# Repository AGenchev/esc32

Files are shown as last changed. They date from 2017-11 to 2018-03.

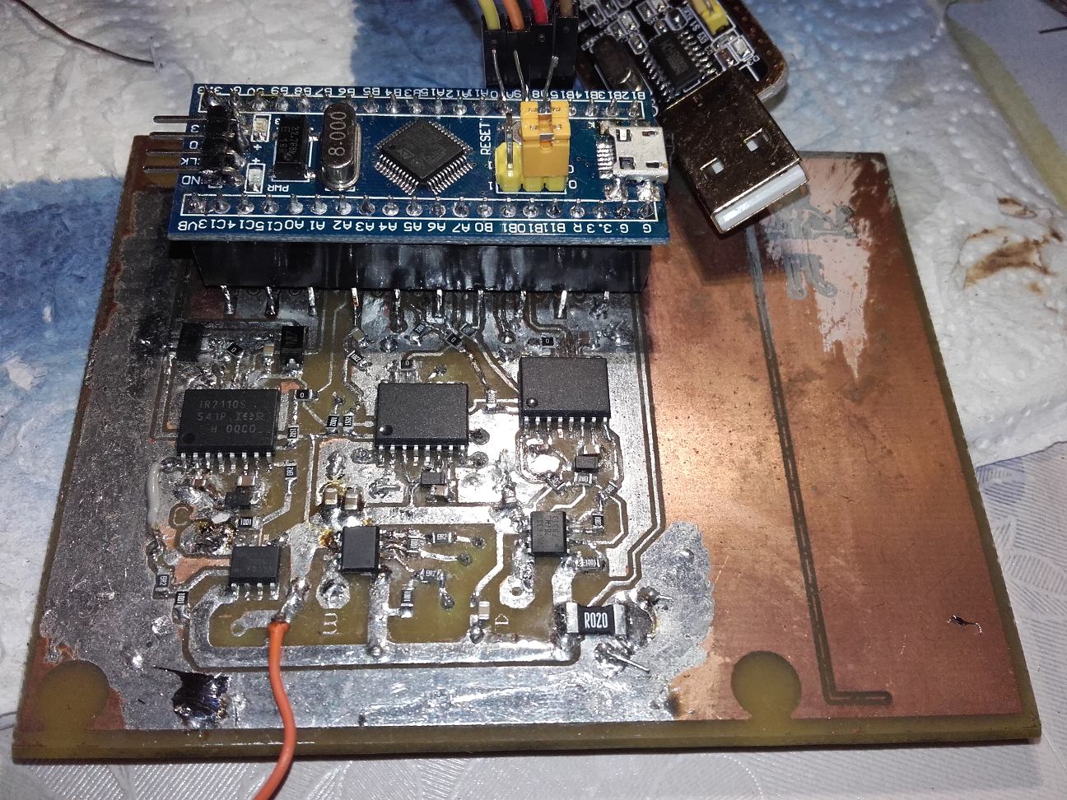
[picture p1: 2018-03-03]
hardware/HardWr_0.2a/images/FirstPrototype-single-layer.jpg

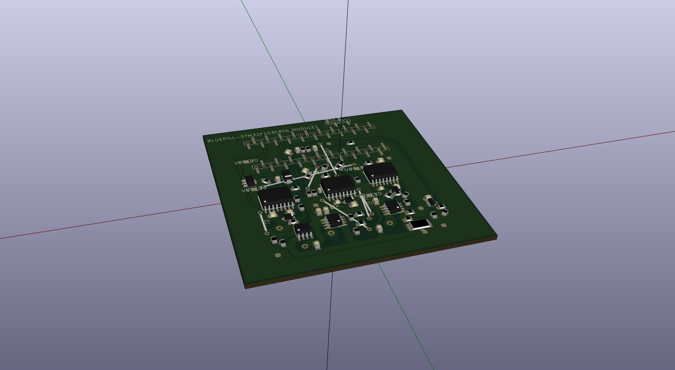
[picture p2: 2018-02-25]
hardware/HardWr_0.2a/images/HardWr_v.02b.png

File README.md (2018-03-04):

# code taken from esc32, reworked to compile with GCC/freeware toolchain

I modified this and reformed the project... The goal - to compile with FOSS tools completely and to contain all source.
I put in a PCB hardware design to test it.
I probably have introduced new bugs.

First "problem": When I compiled with GCC, I got less CPU free time than the binary from esc32. Thus the control loop was closer to take 100% of the CPU time.
I considered this dangerous, because the control loop is timer-driven, e.t. in IRQ. Resolution path taken: to rewrite the control loop in integer. Most of it's done, RPM calculation is still in floating point though.

The ESC code is in <a href=https://github.com/AGenchev/esc32/tree/gelemod02/onboard>"onboard"</a> directory. <br/>
The <a href=https://github.com/AGenchev/esc32/tree/gelemod02/ground>"ground"</a> directory contains the utility which tunes the rpm PID and the current limiter PID. It does not work yet with my hardware as I have not modified it. Actually I use the ESC with current limiter turned off.

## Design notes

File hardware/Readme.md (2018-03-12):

The hardware was converted from EAGLE to KiCad<br/>
<b>Note:</b> I will post hardware which is not fully compatible with the official code of ESC32.
versions:<br/><br/>
a href=https://github.com/AGenchev/esc32/tree/gelemod02/hardware/HardWr_0.2a>HardWr_0.2</a> is on single-layer (w. bridges) routed PCB. ESC32 works on bluepill.
The CPU is STM32F103C8T6, found on cheap chinese boards called Bluepill.
Uses IR2110S NMOSFET gate drivers.
<br /><b>WARNING:</b> The Vcc of the motor and of the IR2110S is tied together so the Vcc shall not exceed 20V for this project.
<br />Note: My test PCB is not intended to fly or to drive racing car. I just wanted to drive a BLDC motor with fixed RPM indoor. 
<br />Control: over serial interface. I set baudrate to 230400, 8-N-1. PA8 is used as "Device Select", active=1 to enable the serial interface on PA9 & PA10. There are CLI interface and binary interface.
Other interfaces which were supported by ESC32 (CAN bus, OneWire, PWM) are there, but are disabled via #UNDEF directive in config.h. because I don't need 'em.

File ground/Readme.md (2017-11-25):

The code tries to find the coefficients for the PID regulator of the RPM.
It needs to be modified to find the different coefficients for the new integer only PID.
An integer only PID is not implemented yet so this is the original code.

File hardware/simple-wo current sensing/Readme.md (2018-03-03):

This was designed for a friend who wanted simplest design. Current sensing amplifier and shunt were removed.

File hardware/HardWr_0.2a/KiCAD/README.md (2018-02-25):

<h1>Converted to KiCAD</h1>

Library used: https://github.com/JorgeAparicio/libKiCad

For 3D rendering to work, i had to edit '/home/username/.config/kicad/kicad_common' ini file<br/>
the format is ini file, section is [EnvironmentVariables]<br/>
entry is:<br/>
<b>LIBKICAD=/full_path_to_libkicad_main_folder/</b>

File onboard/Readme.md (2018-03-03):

If you compile this code, and you have flashed the official binary of ESC32 before,
you need to clean the flash memory of the MCU and set the config again, because the format of the config data has changed.
Also the hardware is a bit different.
<br /><b>Note:</b> The PI RPM control algorithm has been reworked in integer. The default P & I coefficients are set conservative so not tuned for fast convergence, e.t. it needs 5 seconds to stabilize on a KV920 motor.

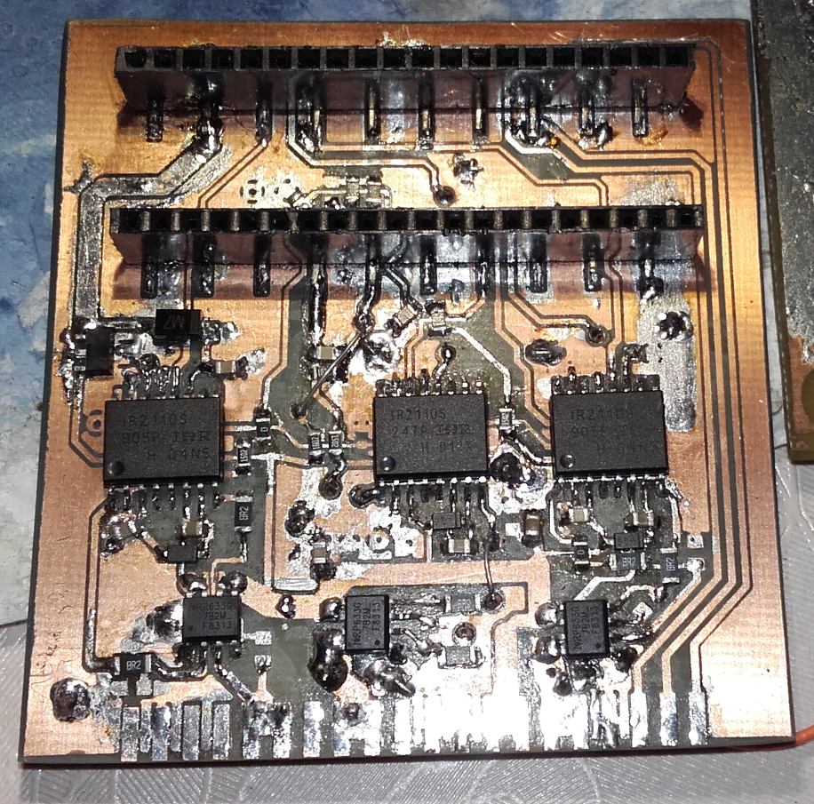
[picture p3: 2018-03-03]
hardware/simple-wo current sensing/Simple-single-layer.jpg

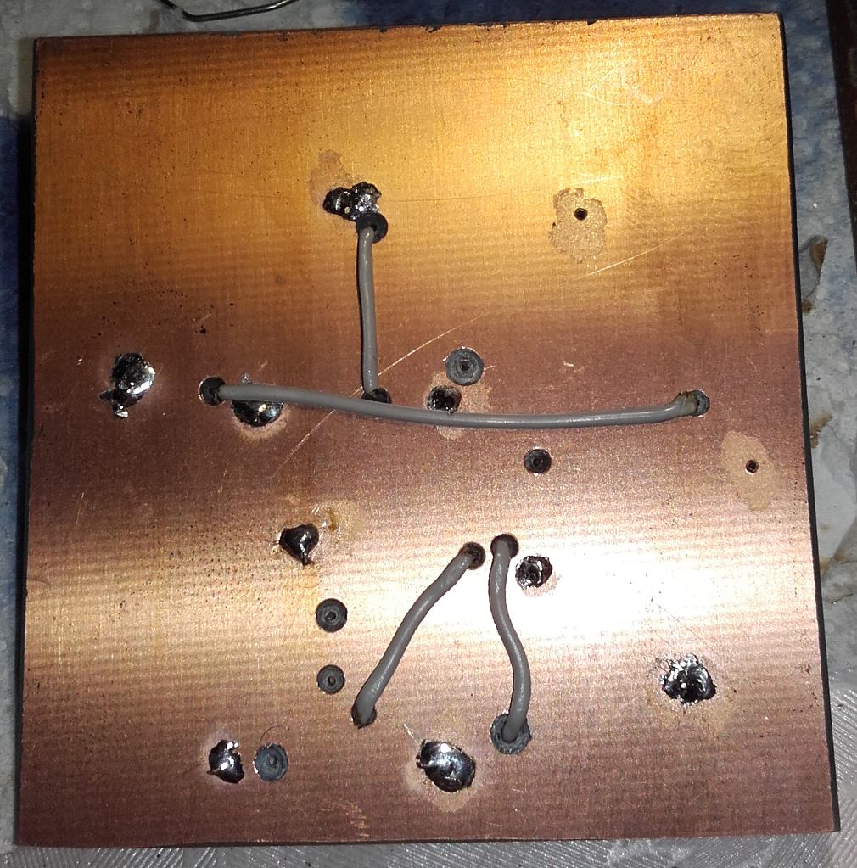
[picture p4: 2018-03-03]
hardware/simple-wo current sensing/Simple-single-layer-BACK.jpg

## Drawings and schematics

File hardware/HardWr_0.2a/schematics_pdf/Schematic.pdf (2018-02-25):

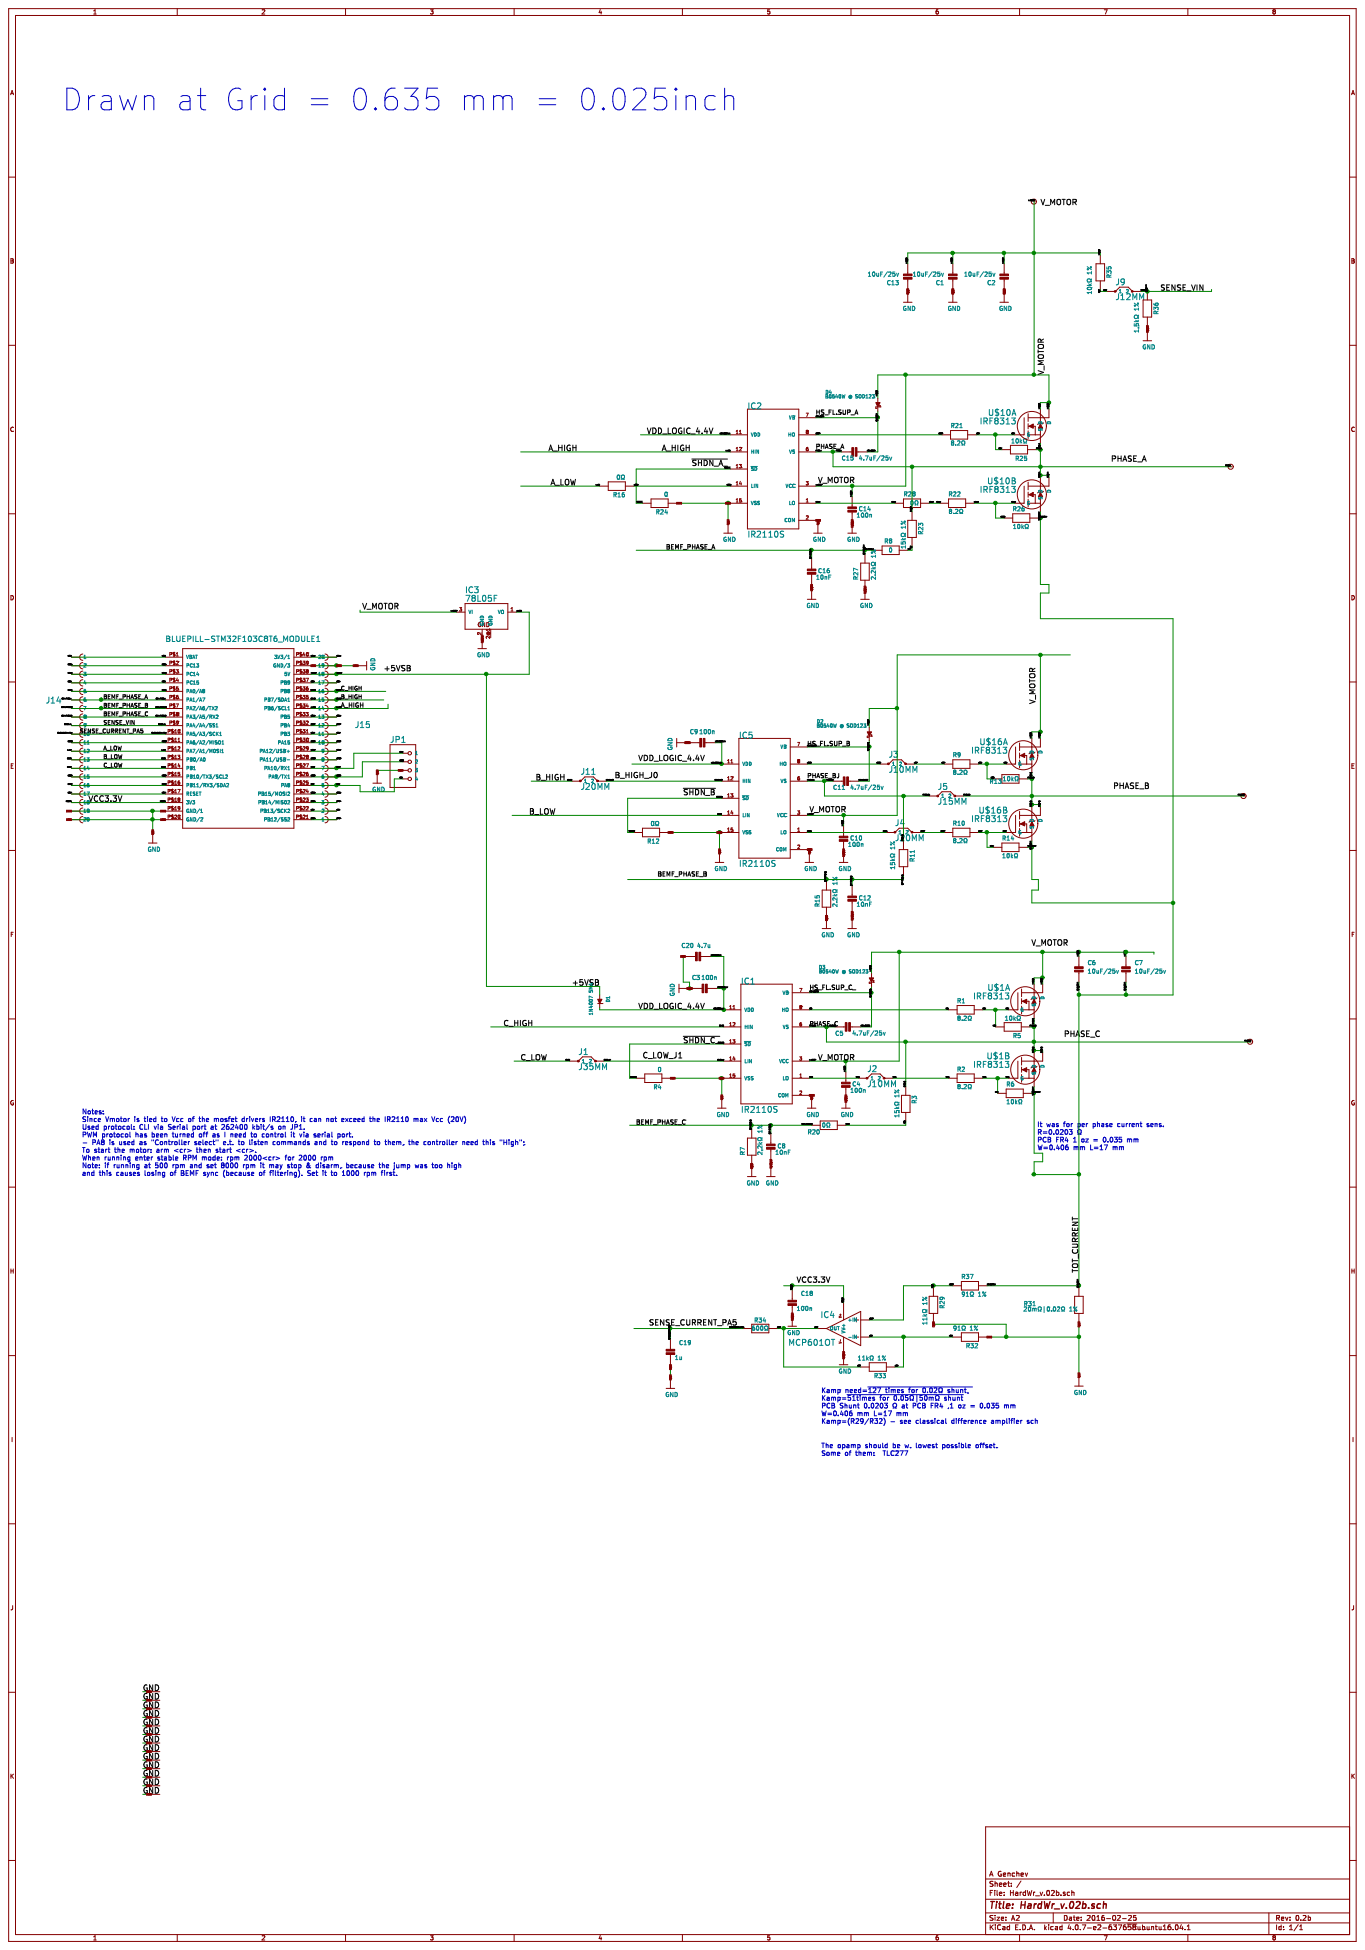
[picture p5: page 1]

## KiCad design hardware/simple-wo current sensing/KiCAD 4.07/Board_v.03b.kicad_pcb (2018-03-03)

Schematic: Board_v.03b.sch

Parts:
C1, C2, C6, C7, C13: 10uF/25v; MICROBUILDER__0805MP
C3: 100n; MICROBUILDER__0805MP
C4, C9, C10, C14: 100n; MICROBUILDER__0603MP
C5, C11, C15: 4.7uF/25v; MICROBUILDER__0805MP
C8, C12, C16: 10nF; MICROBUILDER__0805MP
C20: 4.7u; MICROBUILDER__0805MP
D1: 1N4007 sma; do214ac
D2, D3, D4: SCHOTTKY B0540W@SOD123; sod123
IC1, IC2, IC5: IR2110S; soic-16
J1: J40MM; GELE_V04_J40MM
J3: J5MM; JUMPER_05
J4, J5, J11: J15MM; JUMPER_15
J9: J10MM; JUMPER_10
J14, J15: GELE_V05_CON-20PIN-SMD-MANUALLY-BENT-FROM-NON-SMD
PHASE_C42: PHASE_C; STEVEMARPLE_PAD
R1, R2, R10, R21, R22: 8.2Ω; MICROBUILDER__0805MP
R3, R11, R23: 15kΩ 1%; MICROBUILDER__0805MP
R5, R6, R13, R14, R25, R26: 10kΩ; MICROBUILDER__0805MP
R7, R15, R27: 2.2kΩ 1%; MICROBUILDER__0805MP
R8, R20: 0; MICROBUILDER__0805MP
R9: 8.2; MICROBUILDER__0805MP
R28: 0Ω; MICROBUILDER__0805MP
R35: 10kΩ 1%; MICROBUILDER__0805MP
R36: 1.5kΩ 1%; MICROBUILDER__0805MP
U1: 78L05F; sot89
U$1, U$10, U$16: IRF8313; so-8
U$11, U$30: CON_HEADER_1X20; GELE.TMP_M1X20_SMD_2.54MM_0.1%5c%22_LONGTRACKS
U$36: BLUEPILL; MAPLEMINI_40-DIP-BLUE-PIL
VP_0, VP_1, VP_2, VP_3, VP_4, VP_5, VP_6, VP_7, VP_8, VP_9, VP_10, VP_11: VPDEV0; VPAD_VPAC0
V_MOTOR42: V_MOTOR; STEVEMARPLE_PAD

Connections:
/+5VSB: D1.1 (A), J15.18, U1.1 (VOUT), U$36.P$38 (5V)
/A_HIGH: IC2.12 (HIN), J15.14, U$36.P$34 (PB6/SCL1)
/A_LOW: IC2.14 (LIN), J14.12, U$36.P$12 (PA7/A1/M0SI1)
/BEMF_PHASE_A: C16.2, J14.6, R8.1, R27.2, U$36.P$6 (PA1/A7)
/BEMF_PHASE_B: C12.2, J14.7, R11.2, R15.2, U$36.P$7 (PA2/A6/TX2)
/BEMF_PHASE_C: C8.2, J14.8, R7.2, R20.2, U$36.P$8 (PA3/A5/RX2)
/B_HIGH: J11.1, J15.15, U$36.P$35 (PB7/SDA1)
/B_HIGH_J0: IC5.12 (HIN), J11.2
/B_LOW: IC5.14 (LIN), J14.13, U$36.P$13 (PB0/A0)
/C_HIGH: IC1.12 (HIN), J15.16, U$36.P$36 (PB8)
/C_LOW: J1.1, J14.14, U$36.P$14 (PB1)
/C_LOW_J1: IC1.14 (LIN), J1.2
/DEV_SEL: J15.5, U$30.20, U$36.P$25 (PA8)
/HS_FL.SUP_A: C15.1, D4.2 (K), IC2.7 (VB)
/HS_FL.SUP_B: C11.1, D2.2 (K), IC5.7 (VB)
/HS_FL.SUP_C_: C5.1, D3.2 (K), IC1.7 (VB)
/N$1: R1.2, R5.2, U$1.4 (G)
/N$2: J3.2, R9.1
/N$3: R2.2, R6.1, U$1.2 (G)
/N$4: IC1.8 (HO), R1.1
/N$5: IC1.1 (LO), R2.1
/N$7: R8.2, R23.2
/N$8: R3.2, R20.1
/N$9: R9.2, R13.2, U$16.4 (G)
/N$10: IC5.8 (HO), J3.1
/N$11: R10.2, R14.1, U$16.2 (G)
/N$12: J4.2, R10.1
/N$13: IC5.1 (LO), J4.1
/N$17: R21.2, R25.2, U$10.4 (G)
/N$18: R22.2, R26.1, U$10.2 (G)
/N$19: IC2.8 (HO), R21.1
/N$20: R22.1, R28.2
/N$23: IC2.1 (LO), R28.1
/N$25: J14.5, U$36.P$5 (PA0/A8)
/N$27: J9.1, R35.2
/N$34: J14.1, U$36.P$1 (VBAT)
/N$35: J14.2, U$36.P$2 (PC13)
/N$36: J14.3, U$36.P$3 (PC14)
/N$37: J14.4, U$36.P$4 (PC15)
/N$38: J14.11, U$36.P$11 (PA6/A2/MISO1)
/N$39: J14.15, U$36.P$15 (PB10/TX3/SCL2)
/N$40: J14.16, U$36.P$16 (PB11/RX3/SDA2)
/N$41: J14.17, U$36.P$17 (RESET)
/N$43: J15.1, U$36.P$21 (PB12/SS2)
/N$44: J15.2, U$36.P$22 (PB13/SCK2)
/N$45: J15.3, U$36.P$23 (PB14/MIS02)
/N$46: J15.4, U$36.P$24 (PB15/MOSI2)
/N$48: J15.8, U$36.P$28 (PA11/USB-)
/N$49: J15.9, U$36.P$29 (PA12/USB+)
/N$50: J15.10, U$36.P$30 (PA15)
/N$51: J15.11, U$36.P$31 (PB3)
/N$52: J15.12, U$36.P$32 (PB4)
/N$53: J15.13, U$36.P$33 (PB5)
/N$54: J15.17, U$36.P$37 (PB9)
/N$55: J15.20, U$36.P$40 (3V3/1)
/PHASE_A: C15.2, IC2.6 (VS), PHASE_C42.1, R23.1, R25.1, U$10.3 (S), U$10.7 (D), U$10.8 (D), U$30.15, U$30.16
/PHASE_B: J5.2, R13.1, U$16.3 (S), U$16.7 (D), U$16.8 (D), U$30.8, U$30.9
/PHASE_BJ: C11.2, IC5.6 (VS), J5.1, R11.1
/PHASE_C: C5.2, IC1.6 (VS), R3.1, R5.1, U$1.3 (S), U$1.7 (D), U$1.8 (D), U$30.5, U$30.6
/RXD: J15.7, U$30.18, U$36.P$27 (PA10/RX1)
/SENSE_CURRENT_PA5: J14.10, U$36.P$10 (PA5/A3/SCK1)
/SENSE_VIN: J9.2, J14.9, R36.1, U$36.P$9 (PA4/A4/SS1)
/TXD: J15.6, U$30.19, U$36.P$26 (PA9/TX1)
/VCC3.3V: J14.18, U$36.P$18 (3V3)
/VDD_LOGIC_5V: C3.2, C9.2, C20.2, D1.2 (K), IC1.11 (VDD), IC2.11 (VDD), IC5.11 (VDD)
/V_MOTOR: C1.2, C2.2, C4.2, C6.1, C7.1, C10.2, C13.2, C14.2, D2.1 (A), D3.1 (A), D4.1 (A), IC1.3 (VCC), IC2.3 (VCC), IC5.3 (VCC), R35.1, U1.3 (VIN), U$1.5 (D), U$1.6 (D), U$10.5 (D), U$10.6 (D), U$16.5 (D), U$16.6 (D), U$30.13, U$30.14, V_MOTOR42.1
GND: C1.1, C2.1, C3.1, C4.1, C6.2, C7.2, C8.1, C9.1, C10.1, C12.1, C13.1, C14.1, C16.1, C20.1, IC1.2 (COM), IC1.13 (~SD), IC1.15 (VSS), IC2.2 (COM), IC2.13 (~SD), IC2.15 (VSS), IC5.2 (COM), IC5.13 (~SD), IC5.15 (VSS), J14.19, J14.20, J15.19, R6.2, R7.1, R14.2, R15.1, R26.2, R27.1, R36.2, U1.2 (REF), U$1.1 (S), U$10.1 (S), U$11.1, U$11.2, U$11.3, U$11.4, U$11.5, U$11.6, U$11.7, U$11.8, U$11.9, U$11.10, U$11.11, U$11.12, U$11.13, U$11.14, U$11.15, U$11.16, U$11.17, U$11.18, U$11.19, U$11.20, U$16.1 (S), U$30.1, U$30.2, U$30.11, U$30.12, U$30.17, U$36.P$19 (GND/1), U$36.P$20 (GND/2), U$36.P$39 (GND/3), VP_0.VP, VP_1.VP, VP_2.VP, VP_3.VP, VP_4.VP, VP_5.VP, VP_6.VP, VP_7.VP, VP_8.VP, VP_9.VP, VP_10.VP, VP_11.VP

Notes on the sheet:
Drawn at Grid = 0.635 mm = 0.025inch
It was for per phase current sens. R=0.0203 Ω PCB FR4 1 oz = 0.035 mm W=0.406 mm L=17 mm

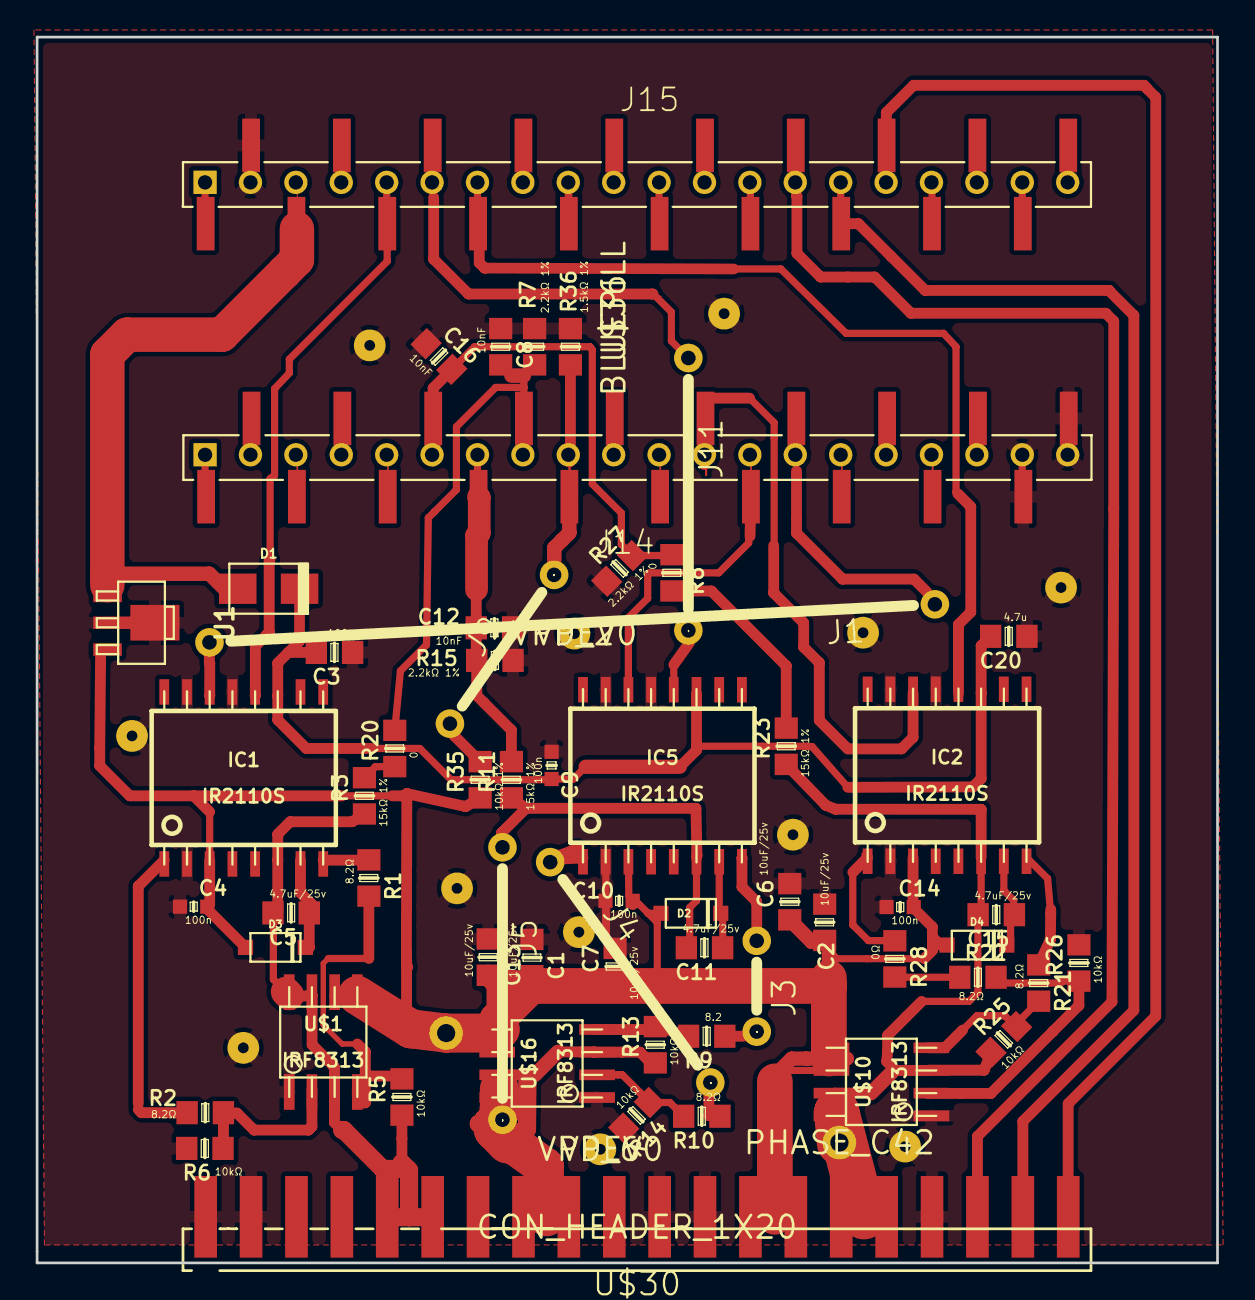
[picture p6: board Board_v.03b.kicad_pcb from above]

Board: 2 copper layers, 66.0 x 68.6 mm, 76 parts (0 on the bottom side), 67 nets.

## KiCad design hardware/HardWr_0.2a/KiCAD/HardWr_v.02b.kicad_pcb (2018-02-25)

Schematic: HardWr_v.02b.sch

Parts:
BLUEPILL-STM32F103C8T6_MODULE1: BLUEPILL; MAPLEMINI_40-DIP-BLUE-PIL
C1, C2, C6, C7, C13: 10uF/25v; c_0805
C3, C4, C18: 100n; c_0805
C5, C11, C15: 4.7uF/25v; c_0805
C8, C12, C16: 10nF; c_0805
C9, C10, C14: 100n; c_0603
C19: 1u; c_0805
C20: 4.7u; c_0805
D1: 1N4007 SMA; do214ac
D2, D3, D4: B0540W @ SOD123; sod123
IC1, IC2, IC5: IR2110S; soic-16
IC3: 78L05F; sot89
IC4: MCP601OT; sot23-5
J1: J35MM; GELE_V04_J35MM
J2, J3: J10MM; JUMPER_10
J4, J11: J20MM; JUMPER_20
J5: J15MM; JUMPER_15
J9: J12MM; JUMPER_12
J14, J15: GELE_V05_CON-20PIN-SMD-MANUALLY-BENT-FROM-NON-SMD
JP1: PINHEAD-2_1X04SMD
PHASE_A42: PHASE_A; STEVEMARPLE_PAD
PHASE_B42: PHASE_B; STEVEMARPLE_PAD
PHASE_C42: PHASE_C; STEVEMARPLE_PAD
R1, R2, R9, R10, R21, R22: 8.2Ω; r_0805
R3, R11, R23: 15kΩ 1%; r_0805
R4, R8, R24: 0; r_0805
R5, R6, R13, R14, R25, R26: 10kΩ; r_0805
R7, R15, R27: 2.2kΩ 1%; r_0805
R12, R16, R20, R28: 0Ω; r_0805
R29, R33: 11kΩ 1%; r_0805
R31: 20mΩ|0.02Ω 1%; r_2512
R32, R37: 91Ω 1%; r_0805
R34: 600Ω; r_0805
R35: 10kΩ 1%; r_0805
R36: 1.5kΩ 1%; r_0805
U$1, U$10, U$16: IRF8313; so-8
VP_0, VP_1, VP_2, VP_3, VP_4, VP_5, VP_6, VP_7, VP_8, VP_9, VP_10, VP_11, VP_12: VPDEV0; VPAD_VPAC0
V_MOTOR42: V_MOTOR; STEVEMARPLE_PAD

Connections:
/+5VSB: BLUEPILL-STM32F103C8T6_MODULE1.P$38 (5V), D1.1 (A), IC3.1 (VO), J15.18
/A_HIGH: BLUEPILL-STM32F103C8T6_MODULE1.P$34 (PB6/SCL1), IC2.12 (HIN), J15.14
/A_LOW: BLUEPILL-STM32F103C8T6_MODULE1.P$12 (PA7/A1/M0SI1), J14.12, R16.2
/BEMF_PHASE_A: BLUEPILL-STM32F103C8T6_MODULE1.P$6 (PA1/A7), C16.2, J14.6, R8.1, R27.2
/BEMF_PHASE_B: BLUEPILL-STM32F103C8T6_MODULE1.P$7 (PA2/A6/TX2), C12.2, J14.7, R11.2, R15.2
/BEMF_PHASE_C: BLUEPILL-STM32F103C8T6_MODULE1.P$8 (PA3/A5/RX2), C8.2, J14.8, R7.2, R20.2
/B_HIGH: BLUEPILL-STM32F103C8T6_MODULE1.P$35 (PB7/SDA1), J11.1, J15.15
/B_HIGH_J0: IC5.12 (HIN), J11.2
/B_LOW: BLUEPILL-STM32F103C8T6_MODULE1.P$13 (PB0/A0), IC5.14 (LIN), J14.13
/C_HIGH: BLUEPILL-STM32F103C8T6_MODULE1.P$36 (PB8), IC1.12 (HIN), J15.16
/C_LOW: BLUEPILL-STM32F103C8T6_MODULE1.P$14 (PB1), J1.1, J14.14
/C_LOW_J1: IC1.14 (LIN), J1.2
/HS_FL.SUP_A: C15.1, D4.2 (K), IC2.7 (VB)
/HS_FL.SUP_B: C11.1, D2.2 (K), IC5.7 (VB)
/HS_FL.SUP_C_: C5.1, D3.2 (K), IC1.7 (VB)
/N$1: R1.2, R5.2, U$1.4 (G)
/N$2: J3.2, R9.1
/N$3: R2.2, R6.1, U$1.2 (G)
/N$4: IC1.8 (HO), R1.1
/N$5: J2.2, R2.1
/N$6: IC1.1 (LO), J2.1
/N$7: R8.2, R23.2
/N$8: R3.2, R20.1
/N$9: R9.2, R13.2, U$16.4 (G)
/N$10: IC5.8 (HO), J3.1
/N$11: R10.2, R14.1, U$16.2 (G)
/N$12: J4.2, R10.1
/N$13: IC5.1 (LO), J4.1
/N$14: IC4.4 (-IN), R32.2, R33.1
/N$17: R21.2, R25.2, U$10.4 (G)
/N$18: R22.2, R26.1, U$10.2 (G)
/N$19: IC2.8 (HO), R21.1
/N$20: R22.1, R28.2
/N$23: IC2.1 (LO), R28.1
/N$24: IC4.1 (OUT), R33.2, R34.1
/N$25: BLUEPILL-STM32F103C8T6_MODULE1.P$5 (PA0/A8), J14.5
/N$26: IC2.14 (LIN), R16.1
/N$27: J9.1, R35.2
/N$30: BLUEPILL-STM32F103C8T6_MODULE1.P$26 (PA9/TX1), J15.6, JP1.2
/N$31: BLUEPILL-STM32F103C8T6_MODULE1.P$27 (PA10/RX1), J15.7, JP1.1
/N$32: IC4.3 (+IN), R29.1, R37.1
/N$34: BLUEPILL-STM32F103C8T6_MODULE1.P$1 (VBAT), J14.1
/N$35: BLUEPILL-STM32F103C8T6_MODULE1.P$2 (PC13), J14.2
/N$36: BLUEPILL-STM32F103C8T6_MODULE1.P$3 (PC14), J14.3
/N$37: BLUEPILL-STM32F103C8T6_MODULE1.P$4 (PC15), J14.4
/N$38: BLUEPILL-STM32F103C8T6_MODULE1.P$11 (PA6/A2/MISO1), J14.11
/N$39: BLUEPILL-STM32F103C8T6_MODULE1.P$15 (PB10/TX3/SCL2), J14.15
/N$40: BLUEPILL-STM32F103C8T6_MODULE1.P$16 (PB11/RX3/SDA2), J14.16
/N$41: BLUEPILL-STM32F103C8T6_MODULE1.P$17 (RESET), J14.17
/N$43: BLUEPILL-STM32F103C8T6_MODULE1.P$21 (PB12/SS2), J15.1
/N$44: BLUEPILL-STM32F103C8T6_MODULE1.P$22 (PB13/SCK2), J15.2
/N$45: BLUEPILL-STM32F103C8T6_MODULE1.P$23 (PB14/MIS02), J15.3
/N$46: BLUEPILL-STM32F103C8T6_MODULE1.P$24 (PB15/MOSI2), J15.4
/N$47: BLUEPILL-STM32F103C8T6_MODULE1.P$25 (PA8), J15.5, JP1.4
/N$48: BLUEPILL-STM32F103C8T6_MODULE1.P$28 (PA11/USB-), J15.8
/N$49: BLUEPILL-STM32F103C8T6_MODULE1.P$29 (PA12/USB+), J15.9
/N$50: BLUEPILL-STM32F103C8T6_MODULE1.P$30 (PA15), J15.10
/N$51: BLUEPILL-STM32F103C8T6_MODULE1.P$31 (PB3), J15.11
/N$52: BLUEPILL-STM32F103C8T6_MODULE1.P$32 (PB4), J15.12
/N$53: BLUEPILL-STM32F103C8T6_MODULE1.P$33 (PB5), J15.13
/N$54: BLUEPILL-STM32F103C8T6_MODULE1.P$37 (PB9), J15.17
/N$55: BLUEPILL-STM32F103C8T6_MODULE1.P$40 (3V3/1), J15.20
/PHASE_A: C15.2, IC2.6 (VS), PHASE_C42.1, R23.1, R25.1, U$10.3 (S), U$10.7 (D), U$10.8 (D)
/PHASE_B: J5.2, PHASE_B42.1, R13.1, U$16.3 (S), U$16.7 (D), U$16.8 (D)
/PHASE_BJ: C11.2, IC5.6 (VS), J5.1, R11.1
/PHASE_C: C5.2, IC1.6 (VS), PHASE_A42.1, R3.1, R5.1, U$1.3 (S), U$1.7 (D), U$1.8 (D)
/SENSE_CURRENT_PA5: BLUEPILL-STM32F103C8T6_MODULE1.P$10 (PA5/A3/SCK1), C19.2, J14.10, R34.2
/SENSE_VIN: BLUEPILL-STM32F103C8T6_MODULE1.P$9 (PA4/A4/SS1), J9.2, J14.9, R36.1
/TOT_CURRENT: C6.2, C7.2, R6.2, R14.2, R26.2, R31.1, R37.2, U$1.1 (S), U$10.1 (S), U$16.1 (S)
/VCC3.3V: BLUEPILL-STM32F103C8T6_MODULE1.P$18 (3V3), C18.2, IC4.5 (V+), J14.18
/VDD_LOGIC_4.4V: C3.2, C9.2, C20.2, D1.2 (K), IC1.11 (VDD), IC2.11 (VDD), IC5.11 (VDD)
/V_MOTOR: C1.2, C2.2, C4.2, C6.1, C7.1, C10.2, C13.2, C14.2, D2.1 (A), D3.1 (A), D4.1 (A), IC1.3 (VCC), IC2.3 (VCC), IC3.3 (VI), IC5.3 (VCC), R35.1, U$1.5 (D), U$1.6 (D), U$10.5 (D), U$10.6 (D), U$16.5 (D), U$16.6 (D), V_MOTOR42.1
/~SHDN_A_: IC2.13 (~SD), R24.2
/~SHDN_B: IC5.13 (~SD), R12.2
/~SHDN_C_: IC1.13 (~SD), R4.2
GND: BLUEPILL-STM32F103C8T6_MODULE1.P$19 (GND/1), BLUEPILL-STM32F103C8T6_MODULE1.P$20 (GND/2), BLUEPILL-STM32F103C8T6_MODULE1.P$39 (GND/3), C1.1, C2.1, C3.1, C4.1, C8.1, C9.1, C10.1, C12.1, C13.1, C14.1, C16.1, C18.1, C19.1, C20.1, IC1.2 (COM), IC1.15 (VSS), IC2.2 (COM), IC2.15 (VSS), IC3.2 (GND), IC4.2 (V-), IC5.2 (COM), IC5.15 (VSS), J14.19, J14.20, J15.19, JP1.3, R4.1, R7.1, R12.1, R15.1, R24.1, R27.1, R29.2, R31.2, R32.1, R36.2, VP_0.VP, VP_1.VP, VP_2.VP, VP_3.VP, VP_4.VP, VP_5.VP, VP_6.VP, VP_7.VP, VP_8.VP, VP_9.VP, VP_10.VP, VP_11.VP, VP_12.VP

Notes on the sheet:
Drawn at Grid = 0.635 mm = 0.025inch
It was for per phase current sens. R=0.0203 Ω PCB FR4 1 oz = 0.035 mm W=0.406 mm L=17 mm
Kamp need=~127 times for 0.02Ω shunt, Kamp=~51times for 0.05Ω|50mΩ shunt PCB Shunt 0.0203 Ω at PCB FR4 ,1 oz = 0.035 mm W=0.406 mm L=17 mm Kamp=(R29/R32) - see classical difference amplifier sch
The opamp should be w. lowest possible offset. Some of them: TLC277
Notes: Since Vmotor is tied to Vcc of the mosfet drivers IR2110, it can not exceed the IR2110 max Vcc (20V) Used protocol: CLI via Serial port at 262400 kbit/s on JP1. PWM protocol has been turned off as I need to control it via serial port. - PA8 is used as "Controller select" e.t. to listen comma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

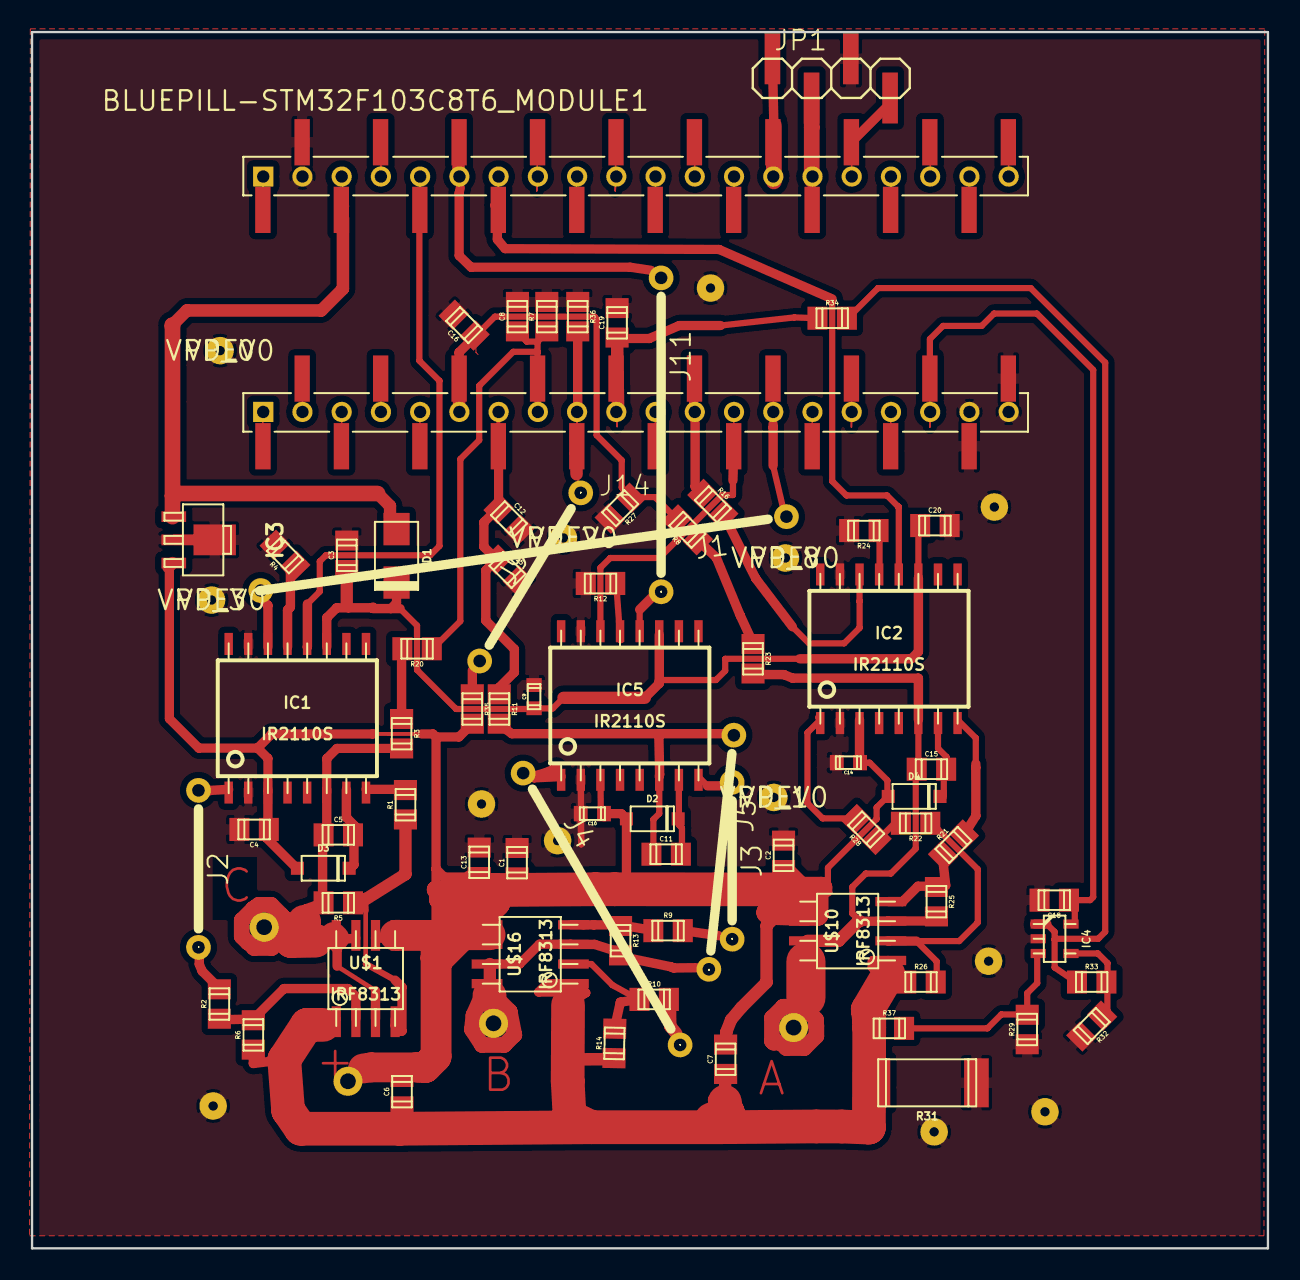
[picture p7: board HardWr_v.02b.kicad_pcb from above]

Board: 2 copper layers, 80.0 x 78.7 mm, 92 parts (0 on the bottom side), 76 nets.

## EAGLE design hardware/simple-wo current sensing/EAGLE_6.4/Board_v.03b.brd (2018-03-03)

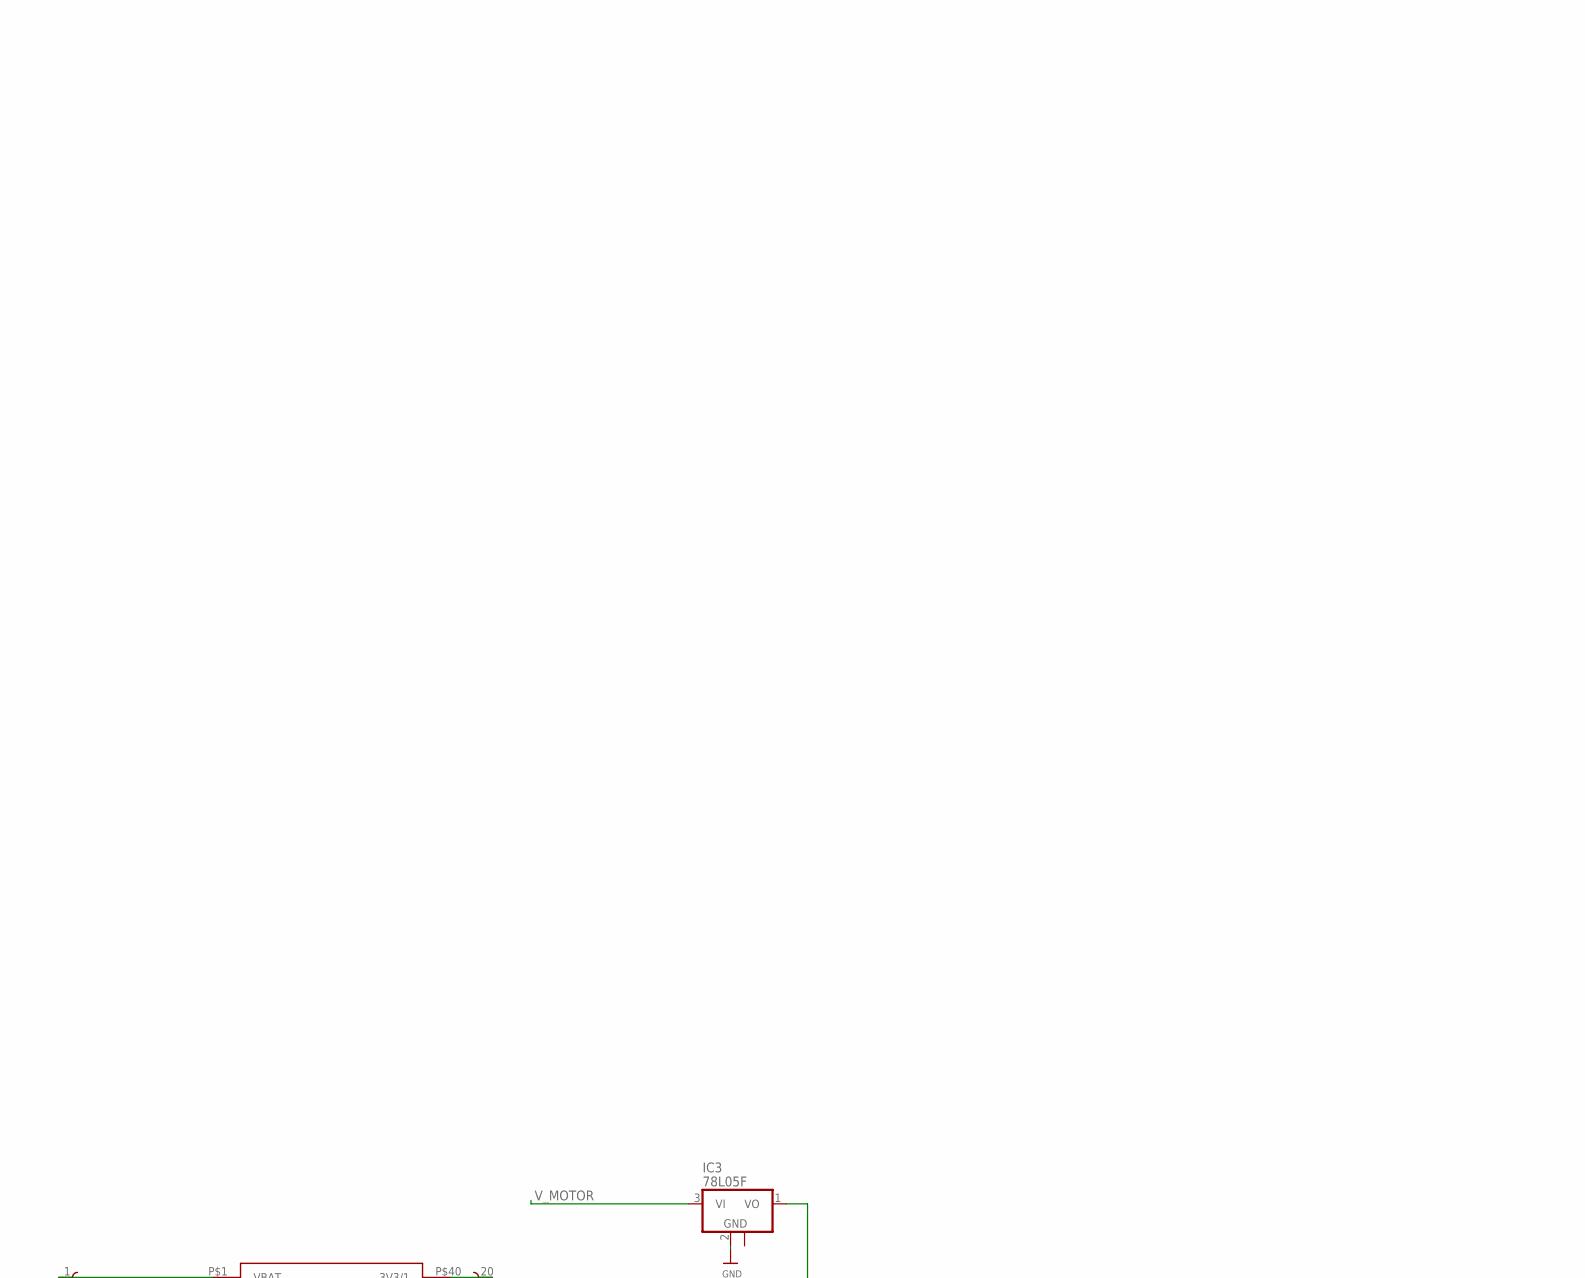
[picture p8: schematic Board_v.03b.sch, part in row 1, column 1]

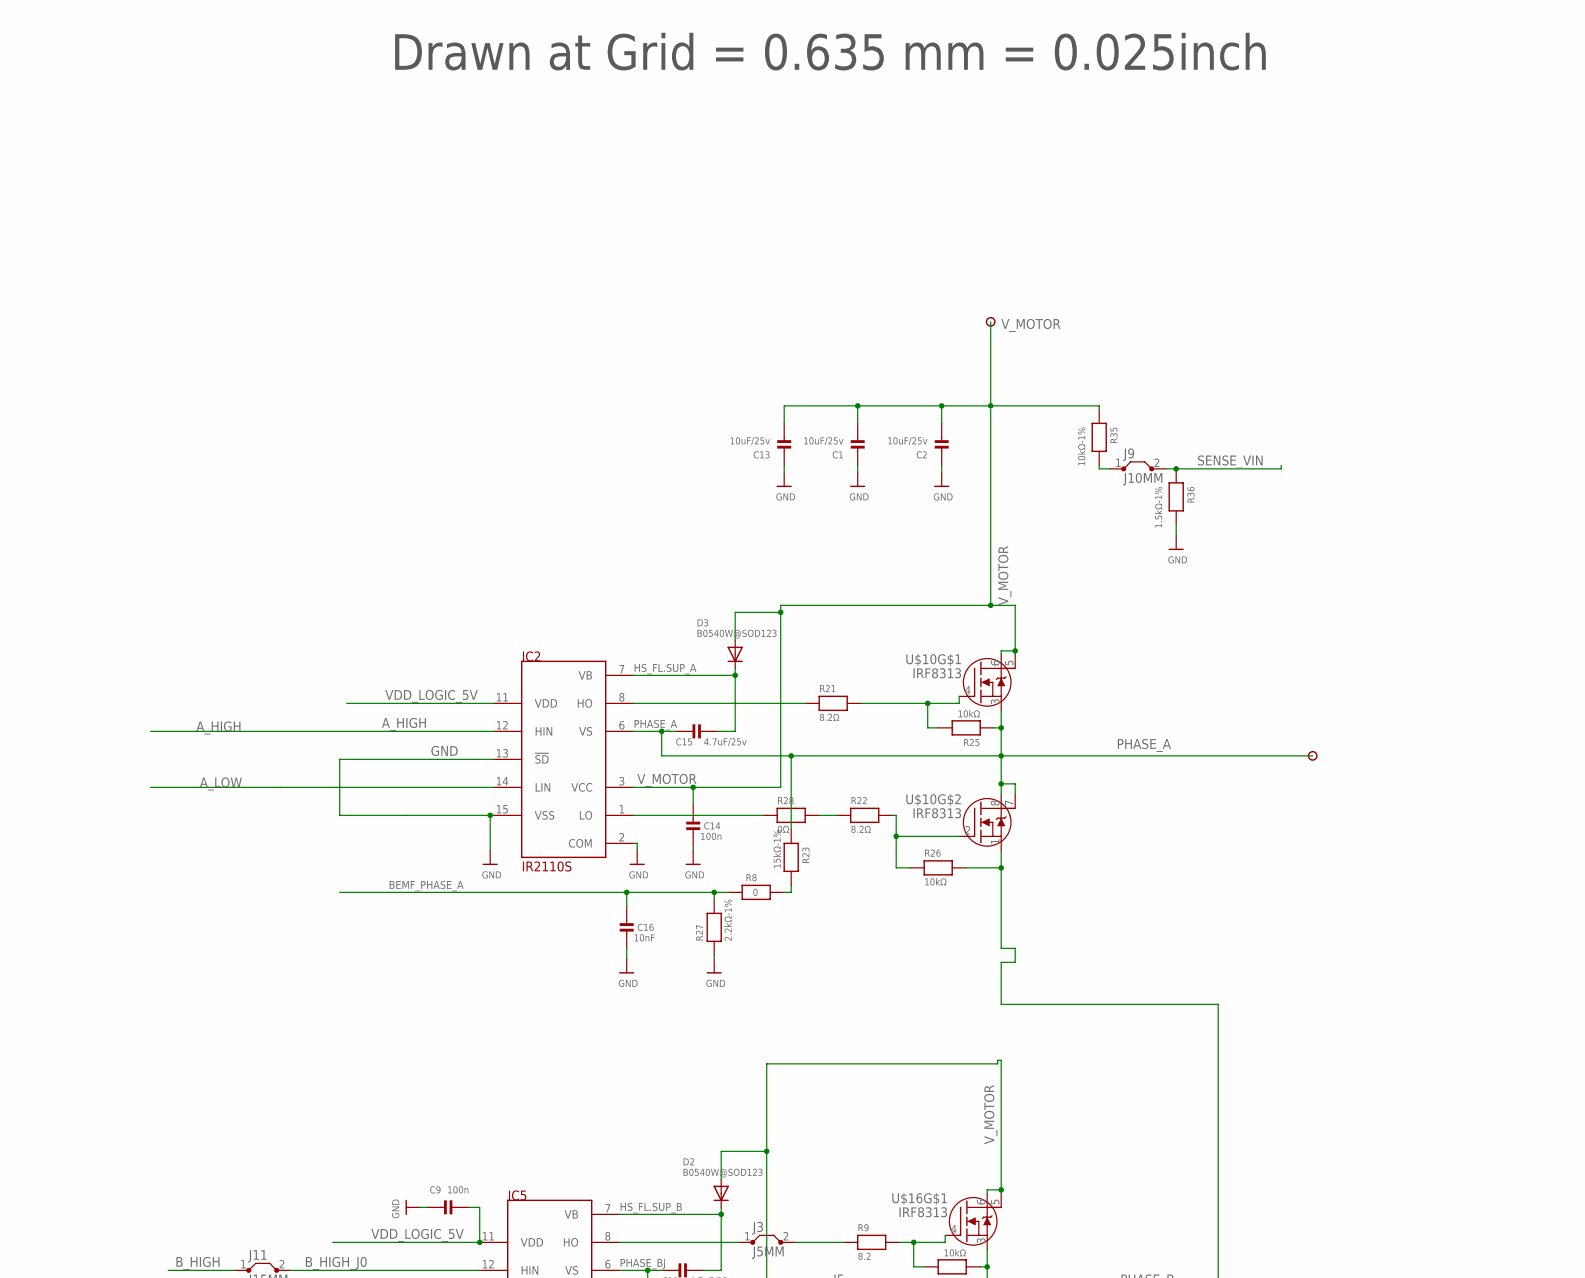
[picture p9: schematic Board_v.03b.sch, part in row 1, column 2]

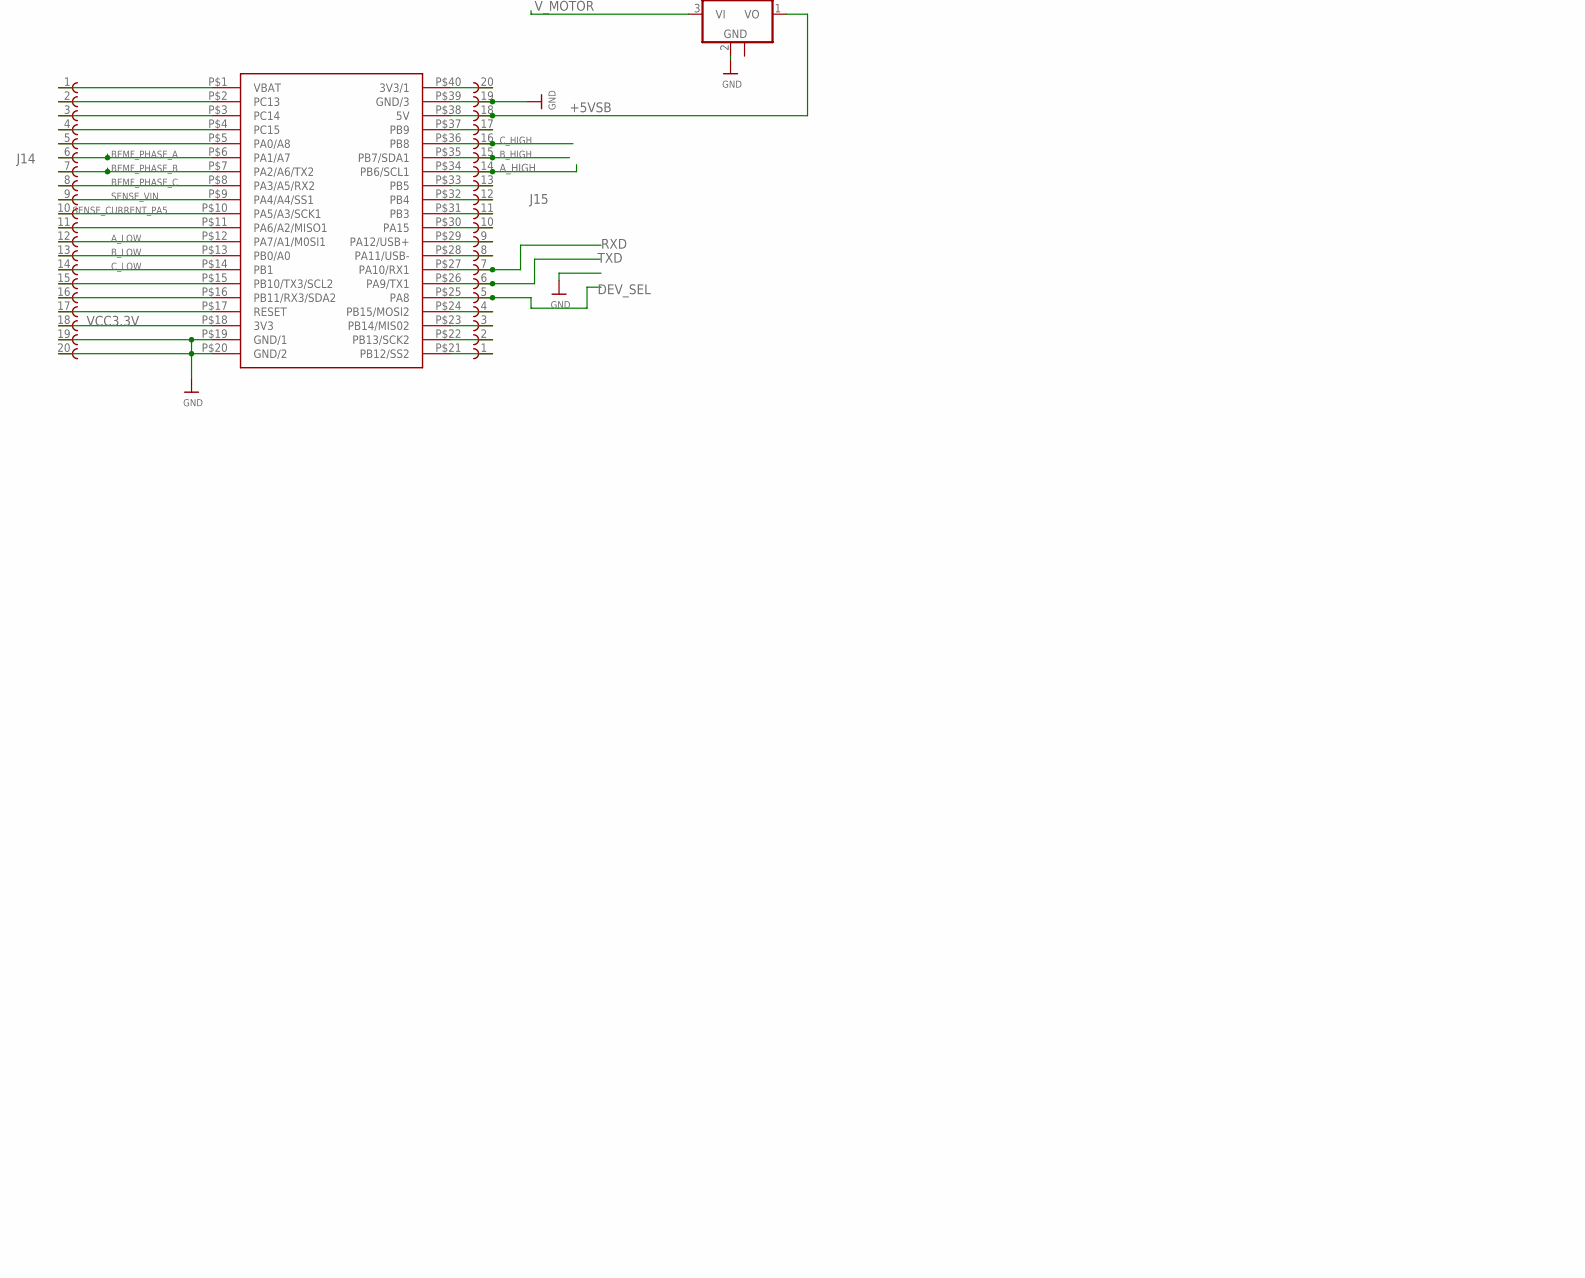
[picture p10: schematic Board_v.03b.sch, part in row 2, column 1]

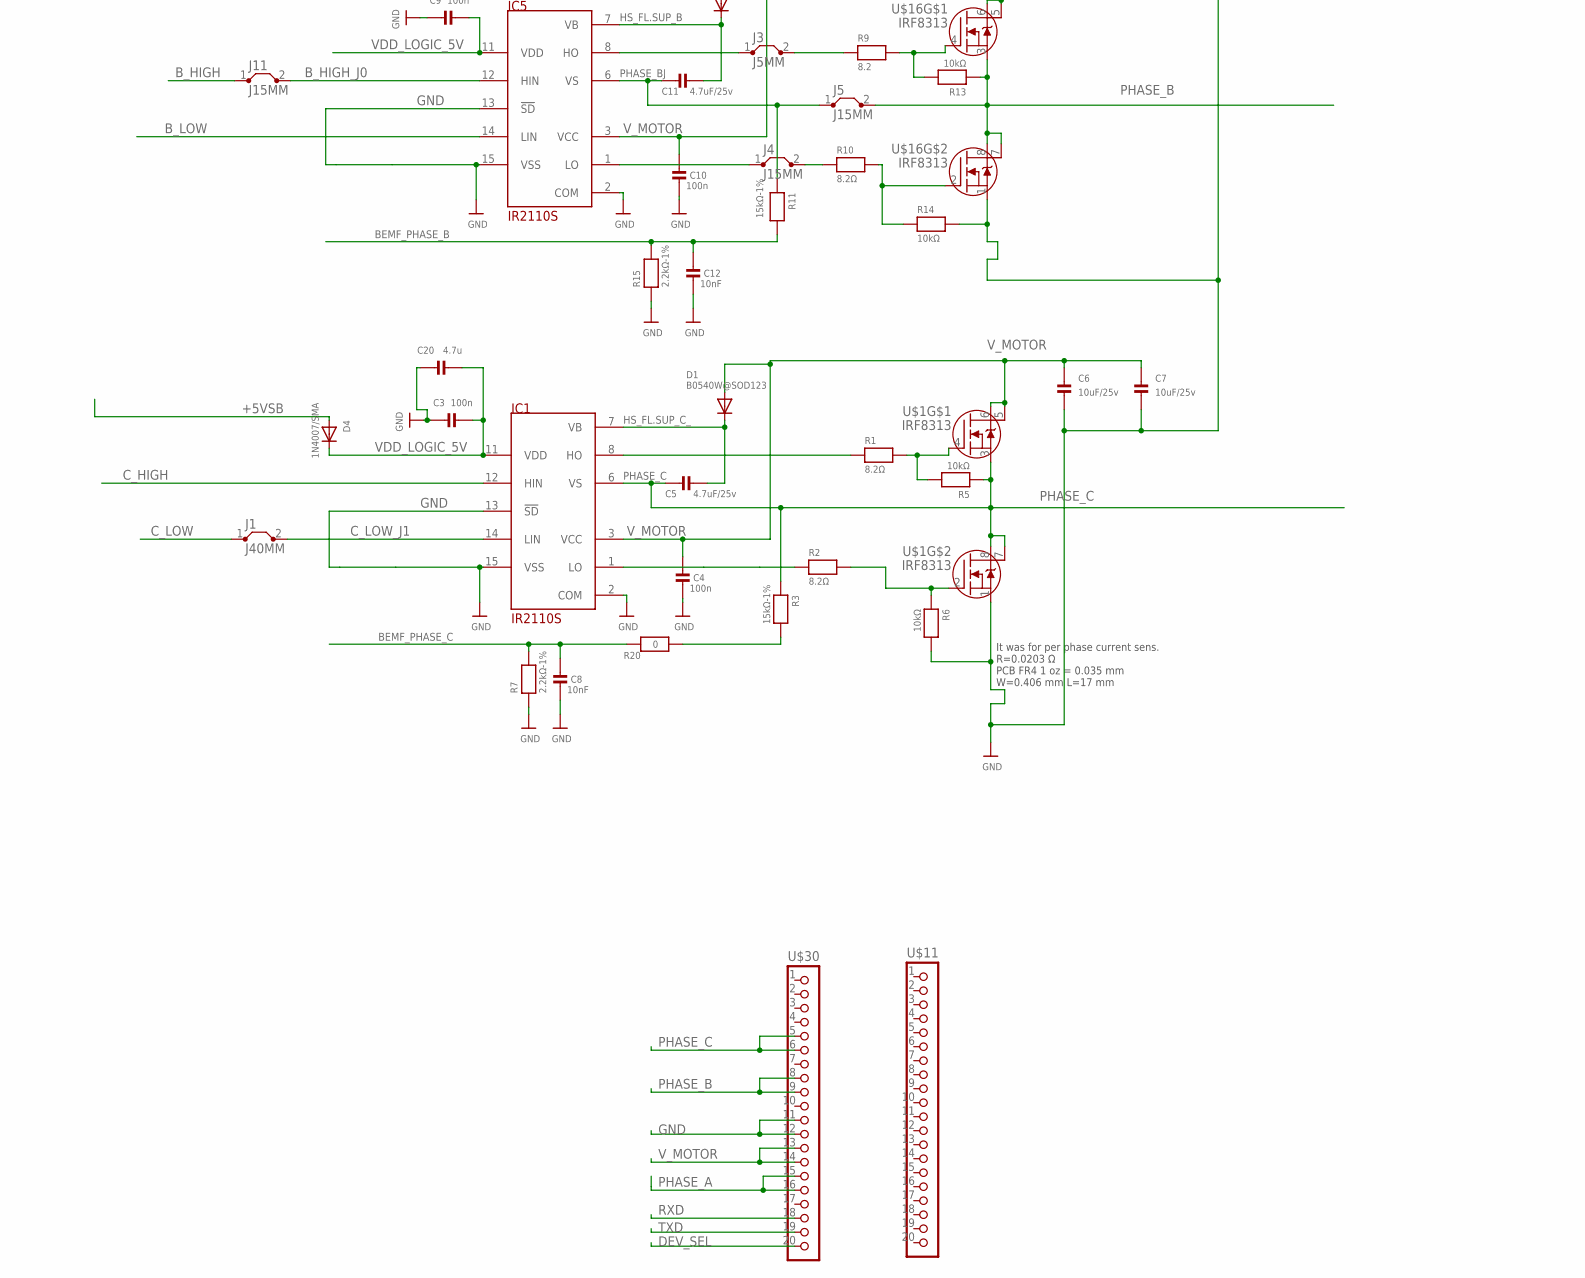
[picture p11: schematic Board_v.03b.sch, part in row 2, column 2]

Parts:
C1, C2, C6, C7, C13: 10uF/25v; _0805MP
C3: 100n; _0805MP
C4, C9, C10, C14: 100n; _0603MP
C5, C11, C15: 4.7uF/25v; _0805MP
C8, C12, C16: 10nF; _0805MP
C20: 4.7u; _0805MP
D1, D2, D3: B0540W@SOD123; SOD-123
D4: 1N4007/SMA; SMADIODE
IC1, IC2, IC5: IR2110S; SO-16DW
IC3: 78L05F; SOT89
J1: J40MM
J3: J5MM; 05
J4, J5, J11: J15MM; 15
J9: J10MM; 10
J14, J15: 61002013321; CON-20PIN-SMD-MANUALLY-BENT-FROM-NON-SMD
PHASE_C: PHASE_C; PAD
R1, R2, R10, R21, R22: 8.2Ω; _0805MP
R3, R11, R23: 15kΩ-1%; _0805MP
R5, R6, R13, R14, R25, R26: 10kΩ; _0805MP
R7, R15, R27: 2.2kΩ-1%; _0805MP
R8, R20: 0; _0805MP
R9: 8.2; _0805MP
R28: 0Ω; _0805MP
R35: 10kΩ-1%; _0805MP
R36: 1.5kΩ-1%; _0805MP
U$1, U$10, U$16: IRF8313; SO08
U$11, U$30: CON_HEADER_1X20; M1X20_SMD_2.54MM/0.1"_LONGTRACKS
U$36: BLUEPILL; 40-DIP-BLUE-PIL
V_MOTOR: V_MOTOR; PAD

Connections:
+5VSB: D4.A, IC3.1 (VO), J15.18, U$36.P$38 (5V)
A_HIGH: IC2.12 (HIN), J15.14, U$36.P$34 (PB6/SCL1)
A_LOW: IC2.14 (LIN), J14.12, U$36.P$12 (PA7/A1/M0SI1)
BEMF_PHASE_A: C16.2, J14.6, R8.1, R27.2, U$36.P$6 (PA1/A7)
BEMF_PHASE_B: C12.2, J14.7, R11.2, R15.2, U$36.P$7 (PA2/A6/TX2)
BEMF_PHASE_C: C8.2, J14.8, R7.2, R20.2, U$36.P$8 (PA3/A5/RX2)
B_HIGH: J11.1, J15.15, U$36.P$35 (PB7/SDA1)
B_HIGH_J0: IC5.12 (HIN), J11.2
B_LOW: IC5.14 (LIN), J14.13, U$36.P$13 (PB0/A0)
C_HIGH: IC1.12 (HIN), J15.16, U$36.P$36 (PB8)
C_LOW: J1.1, J14.14, U$36.P$14 (PB1)
C_LOW_J1: IC1.14 (LIN), J1.2
DEV_SEL: J15.5, U$30.20, U$36.P$25 (PA8)
GND: C1.1, C2.1, C3.1, C4.1, C6.2, C7.2, C8.1, C9.1, C10.1, C12.1, C13.1, C14.1, C16.1, C20.1, IC1.2 (COM), IC1.13 (!SD), IC1.15 (VSS), IC2.2 (COM), IC2.13 (!SD), IC2.15 (VSS), IC3.2 (GND), IC5.2 (COM), IC5.13 (!SD), IC5.15 (VSS), J14.19, J14.20, J15.19, R6.2, R7.1, R14.2, R15.1, R26.2, R27.1, R36.2, U$1.1 (S), U$10.1 (S), U$16.1 (S), U$30.11, U$30.12, U$36.P$19 (GND/1), U$36.P$20 (GND/2), U$36.P$39 (GND/3)
HS_FL.SUP_A: C15.1, D3.C, IC2.7 (VB)
HS_FL.SUP_B: C11.1, D2.C, IC5.7 (VB)
HS_FL.SUP_C_: C5.1, D1.C, IC1.7 (VB)
unnamed: R1.2, R5.2, U$1.4 (G)
unnamed: J3.2, R9.1
unnamed: R2.2, R6.1, U$1.2 (G)
unnamed: IC1.8 (HO), R1.1
unnamed: IC1.1 (LO), R2.1
unnamed: R8.2, R23.2
unnamed: R3.2, R20.1
unnamed: R9.2, R13.2, U$16.4 (G)
unnamed: IC5.8 (HO), J3.1
unnamed: R10.2, R14.1, U$16.2 (G)
unnamed: J4.2, R10.1
unnamed: IC5.1 (LO), J4.1
unnamed: R21.2, R25.2, U$10.4 (G)
unnamed: R22.2, R26.1, U$10.2 (G)
unnamed: IC2.8 (HO), R21.1
unnamed: R22.1, R28.2
unnamed: IC2.1 (LO), R28.1
unnamed: J14.5, U$36.P$5 (PA0/A8)
unnamed: J9.1, R35.2
unnamed: J14.1, U$36.P$1 (VBAT)
unnamed: J14.2, U$36.P$2 (PC13)
unnamed: J14.3, U$36.P$3 (PC14)
unnamed: J14.4, U$36.P$4 (PC15)
unnamed: J14.11, U$36.P$11 (PA6/A2/MISO1)
unnamed: J14.15, U$36.P$15 (PB10/TX3/SCL2)
unnamed: J14.16, U$36.P$16 (PB11/RX3/SDA2)
unnamed: J14.17, U$36.P$17 (RESET)
unnamed: J15.1, U$36.P$21 (PB12/SS2)
unnamed: J15.2, U$36.P$22 (PB13/SCK2)
unnamed: J15.3, U$36.P$23 (PB14/MIS02)
unnamed: J15.4, U$36.P$24 (PB15/MOSI2)
unnamed: J15.8, U$36.P$28 (PA11/USB-)
unnamed: J15.9, U$36.P$29 (PA12/USB+)
unnamed: J15.10, U$36.P$30 (PA15)
unnamed: J15.11, U$36.P$31 (PB3)
unnamed: J15.12, U$36.P$32 (PB4)
unnamed: J15.13, U$36.P$33 (PB5)
unnamed: J15.17, U$36.P$37 (PB9)
unnamed: J15.20, U$36.P$40 (3V3/1)
PHASE_A: C15.2, IC2.6 (VS), PHASE_C.1, R23.1, R25.1, U$10.3 (S), U$10.7 (D), U$10.8 (D), U$30.15, U$30.16
PHASE_B: J5.2, R13.1, U$16.3 (S), U$16.7 (D), U$16.8 (D), U$30.8, U$30.9
PHASE_BJ: C11.2, IC5.6 (VS), J5.1, R11.1
PHASE_C: C5.2, IC1.6 (VS), R3.1, R5.1, U$1.3 (S), U$1.7 (D), U$1.8 (D), U$30.5, U$30.6
RXD: J15.7, U$30.18, U$36.P$27 (PA10/RX1)
SENSE_CURRENT_PA5: J14.10, U$36.P$10 (PA5/A3/SCK1)
SENSE_VIN: J9.2, J14.9, R36.1, U$36.P$9 (PA4/A4/SS1)
TXD: J15.6, U$30.19, U$36.P$26 (PA9/TX1)
VCC3.3V: J14.18, U$36.P$18 (3V3)
VDD_LOGIC_5V: C3.2, C9.2, C20.2, D4.C, IC1.11 (VDD), IC2.11 (VDD), IC5.11 (VDD)
V_MOTOR: C1.2, C2.2, C4.2, C6.1, C7.1, C10.2, C13.2, C14.2, D1.A, D2.A, D3.A, IC1.3 (VCC), IC2.3 (VCC), IC3.3 (VI), IC5.3 (VCC), R35.1, U$1.5 (D), U$1.6 (D), U$10.5 (D), U$10.6 (D), U$16.5 (D), U$16.6 (D), U$30.13, U$30.14, V_MOTOR.1

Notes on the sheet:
Drawn at Grid = 0.635 mm = 0.025inch
It was for per phase current sens. R=0.0203 Ω PCB FR4 1 oz = 0.035 mm W=0.406 mm L=17 mm

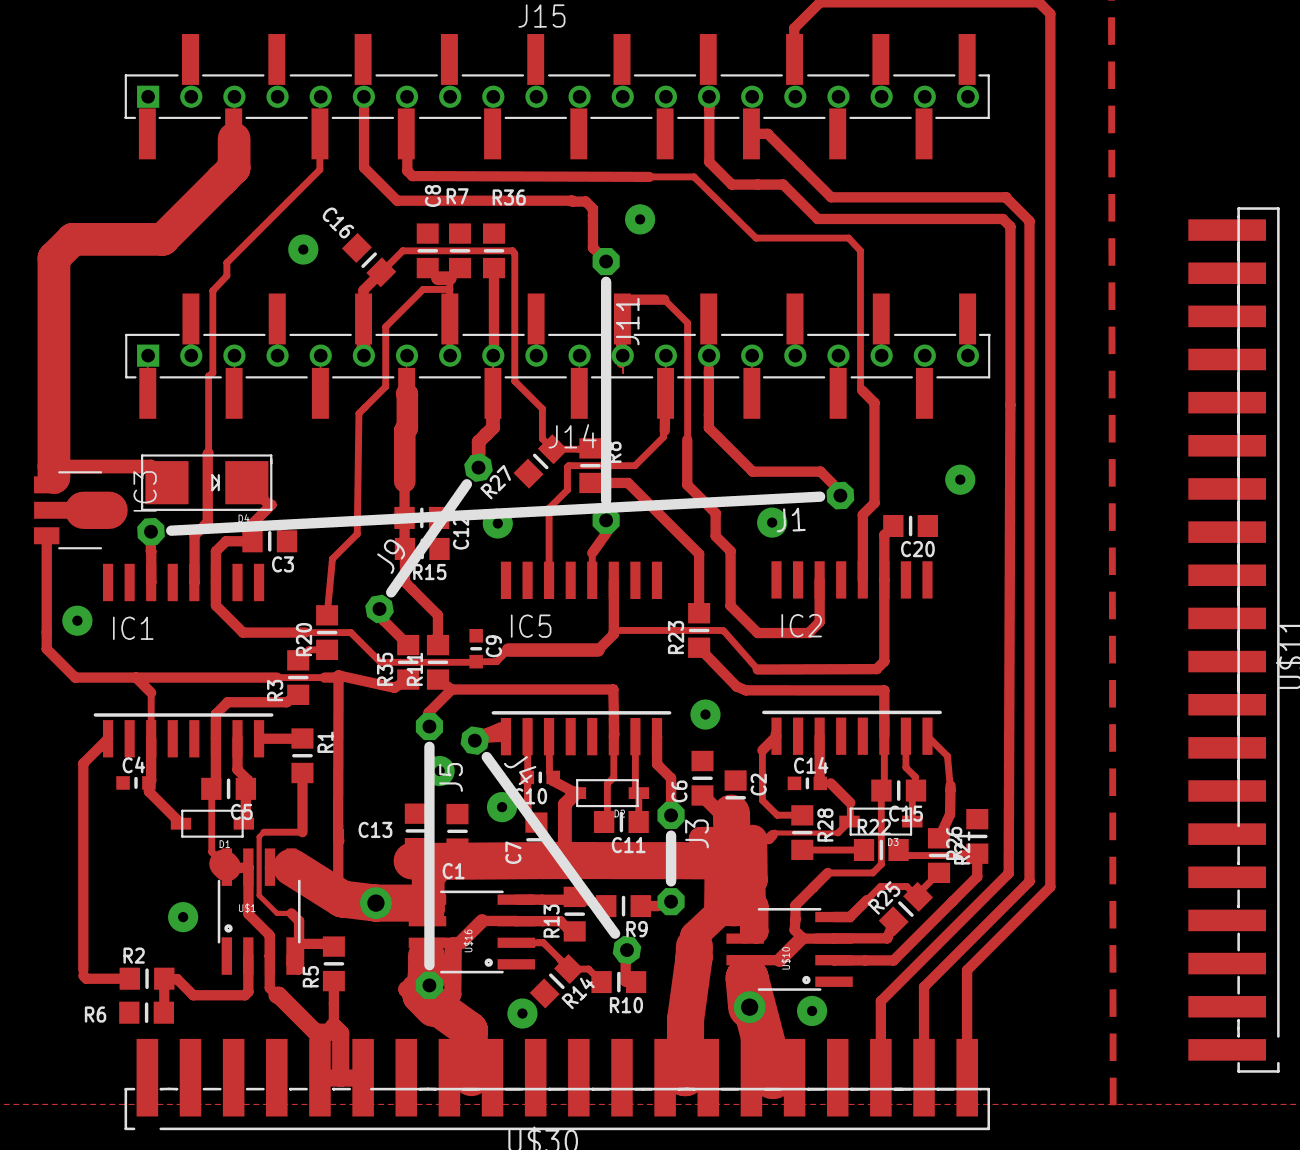
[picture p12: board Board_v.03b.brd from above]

Board: 2 copper layers, 66 parts (0 on the bottom side), 67 nets.

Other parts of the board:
U$13, U$21: MOUNTINGHOLE_2.8

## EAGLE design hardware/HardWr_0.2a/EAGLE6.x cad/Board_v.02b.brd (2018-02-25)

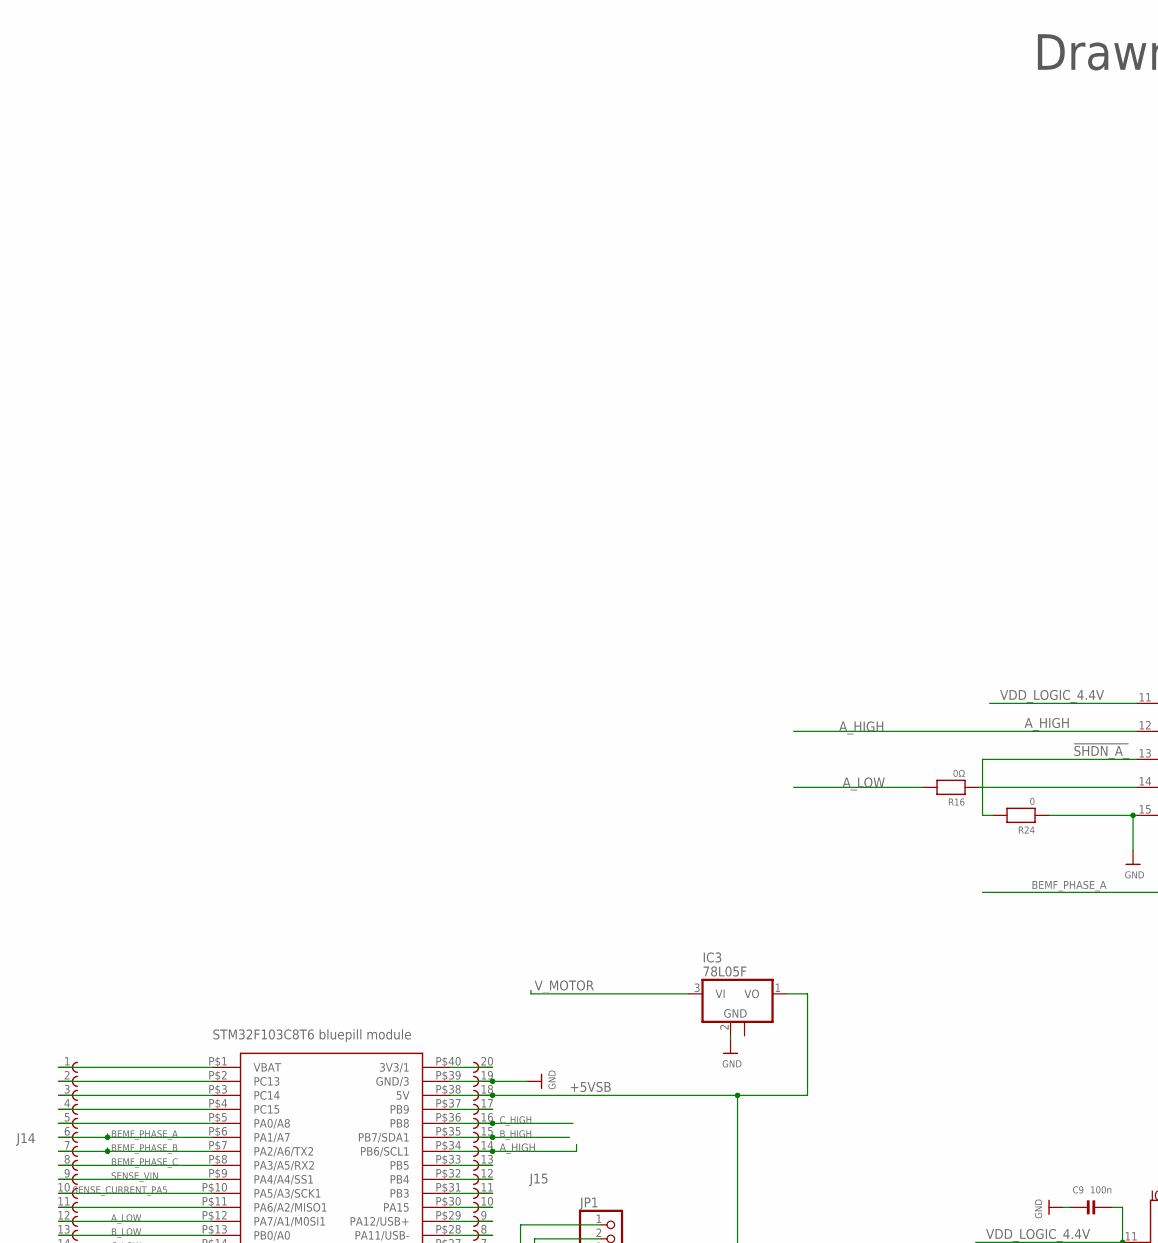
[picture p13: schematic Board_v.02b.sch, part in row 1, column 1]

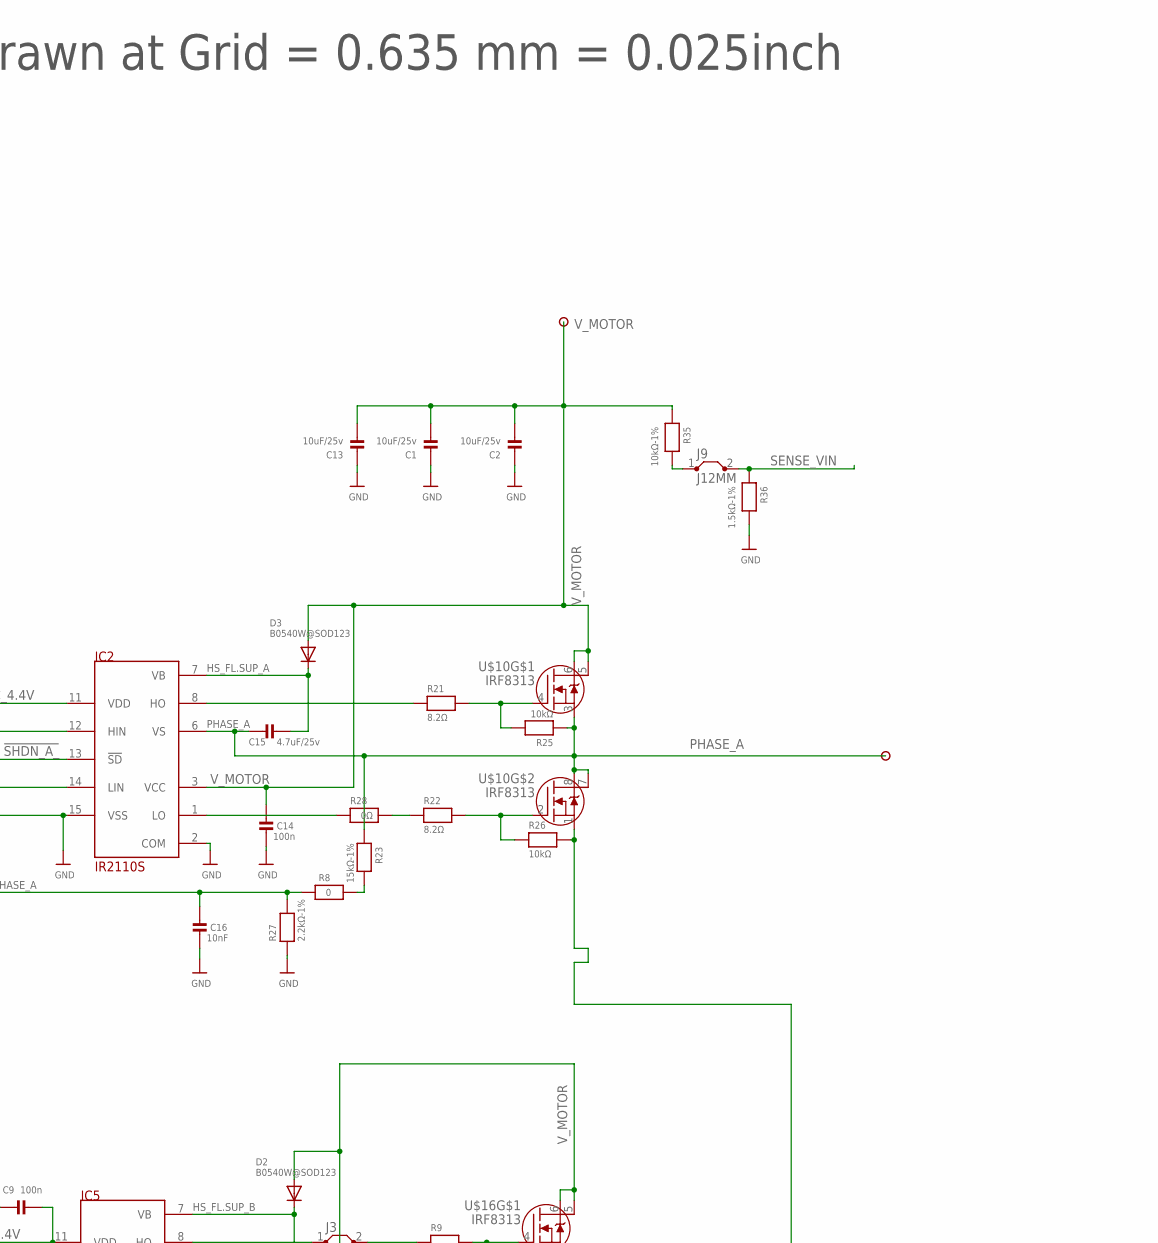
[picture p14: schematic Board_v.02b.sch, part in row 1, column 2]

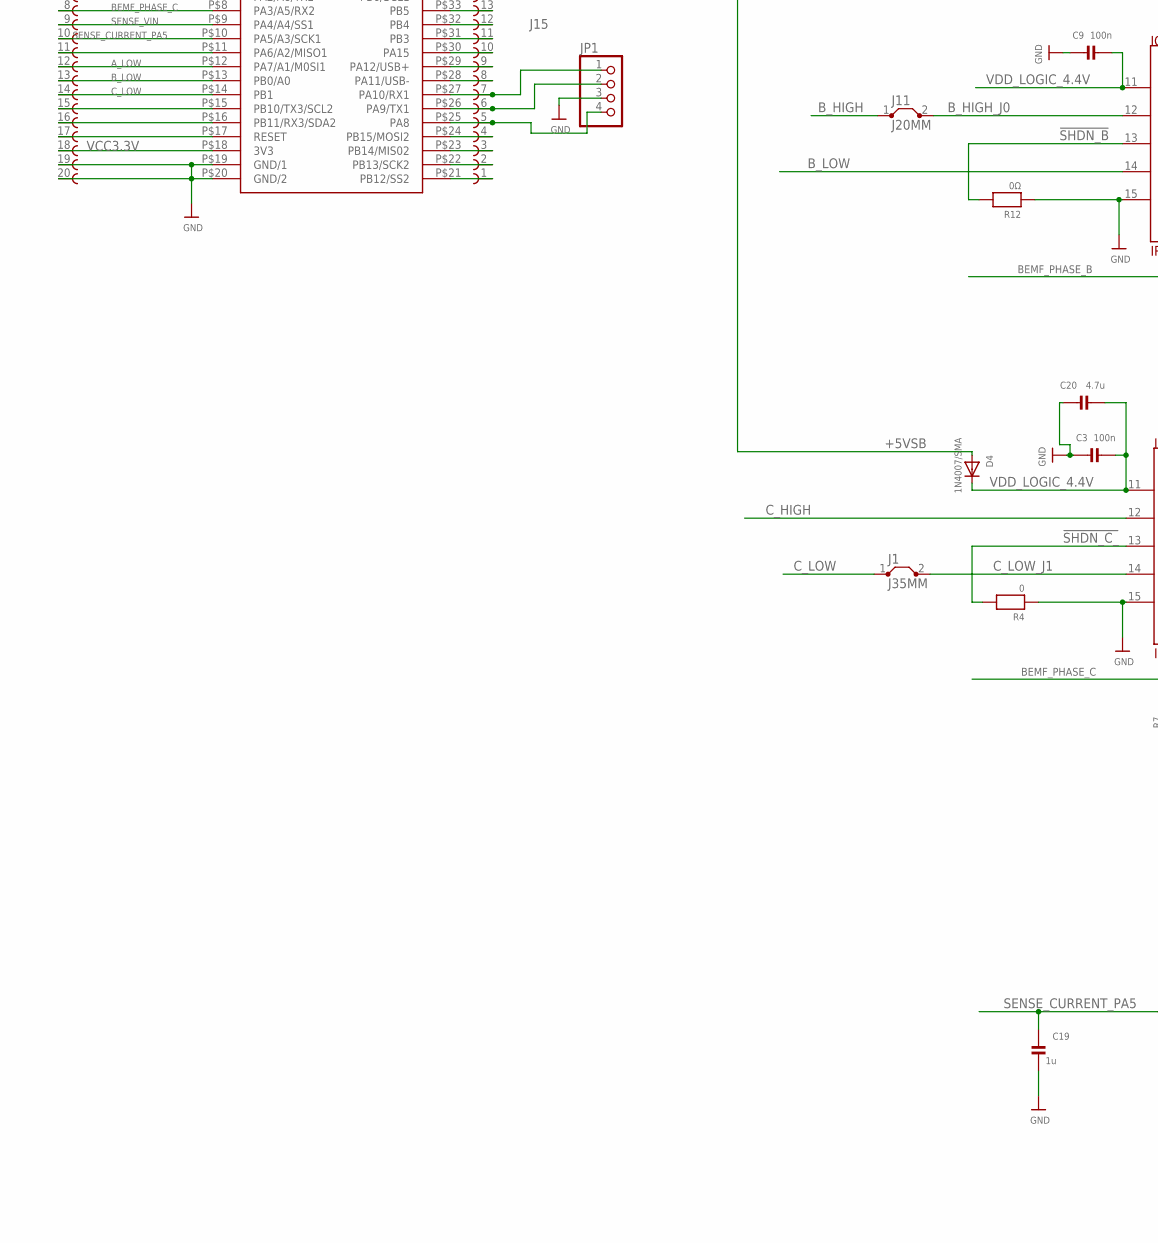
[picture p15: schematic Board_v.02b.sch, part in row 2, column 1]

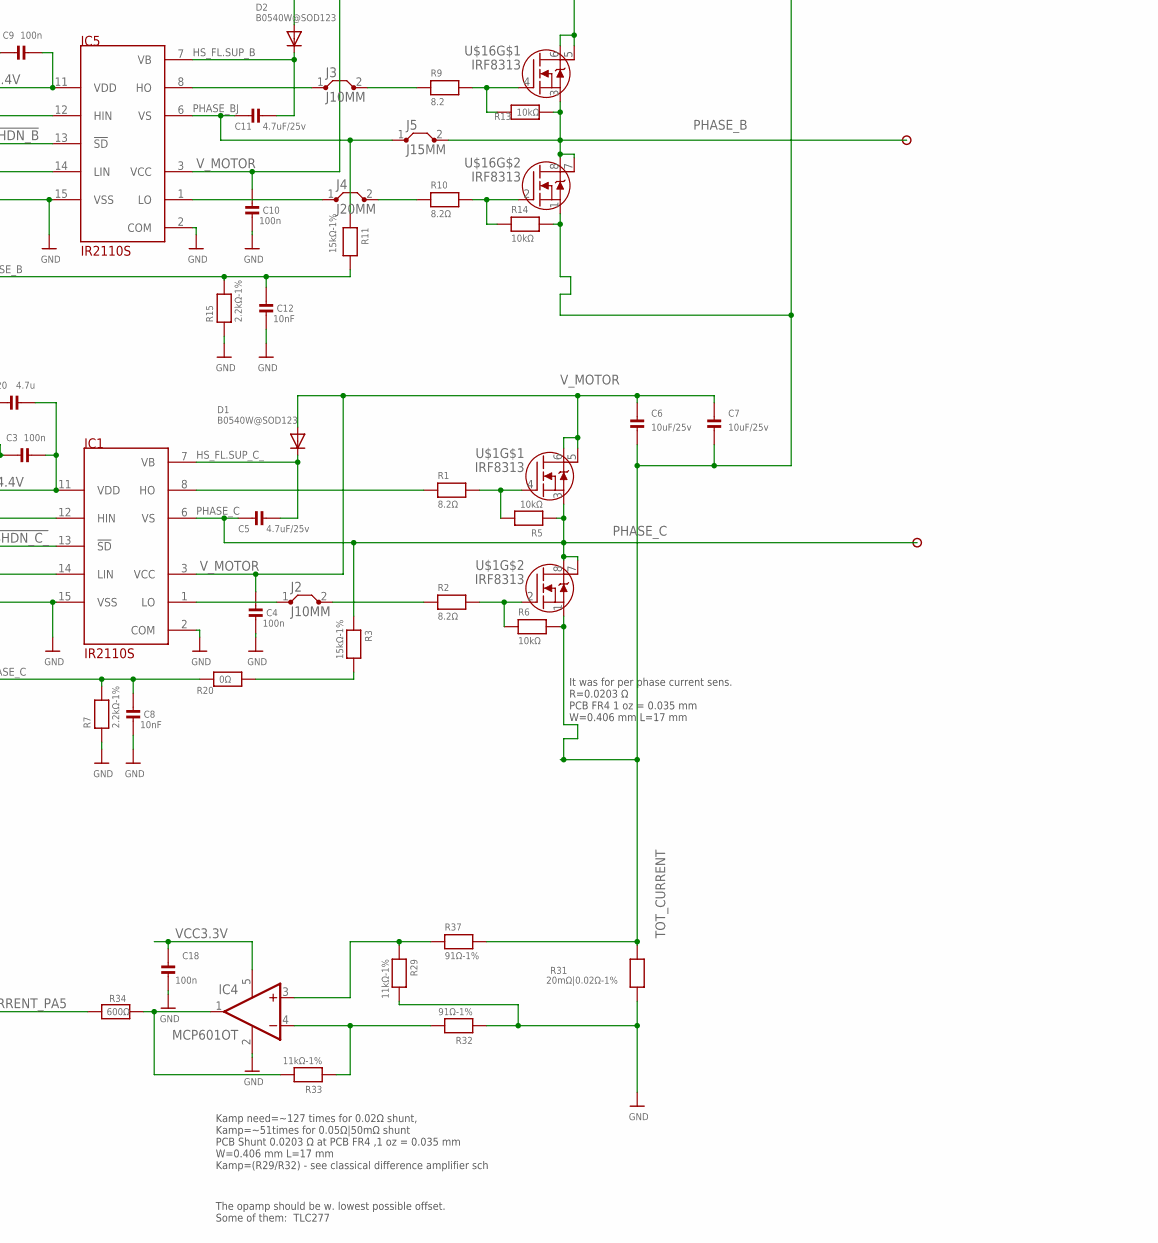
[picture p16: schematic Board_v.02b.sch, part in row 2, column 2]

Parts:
BLUEPILL-STM32F103C8T6_MODULE: BLUEPILL; 40-DIP-BLUE-PIL
C1, C2, C6, C7, C13: 10uF/25v; _0805MP
C3, C18: 100n; _0805MP
C4, C9, C10, C14: 100n; _0603MP
C5, C11, C15: 4.7uF/25v; _0805MP
C8, C12, C16: 10nF; _0805MP
C19: 1u; _0805MP
C20: 4.7u; _0805MP
D1, D2, D3: B0540W@SOD123; SOD-123
D4: 1N4007/SMA; SMADIODE
IC1, IC2, IC5: IR2110S; SO-16DW
IC3: 78L05F; SOT89
IC4: MCP601OT; SOT23-5
J1: J35MM
J2, J3: J10MM; 10
J4, J11: J20MM; 20
J5: J15MM; 15
J9: J12MM; 12
J14, J15: 61002013321; CON-20PIN-SMD-MANUALLY-BENT-FROM-NON-SMD
JP1: PINHD-1X04_2.54-SMD; 1X04SMD
PHASE_A: PHASE_A; PAD
PHASE_B: PHASE_B; PAD
PHASE_C: PHASE_C; PAD
R1, R2, R10, R21, R22: 8.2Ω; _0805MP
R3, R11, R23: 15kΩ-1%; _0805MP
R4, R8, R24: 0; _0805MP
R5, R6, R13, R14, R25, R26: 10kΩ; _0805MP
R7, R15, R27: 2.2kΩ-1%; _0805MP
R9: 8.2; _0805MP
R12, R16, R20, R28: 0Ω; _0805MP
R29, R33: 11kΩ-1%; _0805MP
R31: 20mΩ|0.02Ω-1%; 2512
R32, R37: 91Ω-1%; _0805MP
R34: 600Ω; _0805MP
R35: 10kΩ-1%; _0805MP
R36: 1.5kΩ-1%; _0805MP
U$1, U$10, U$16: IRF8313; SO08
V_MOTOR: V_MOTOR; PAD

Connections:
!SHDN_A_: IC2.13 (!SD), R24.2
!SHDN_B: IC5.13 (!SD), R12.2
!SHDN_C_: IC1.13 (!SD), R4.2
+5VSB: BLUEPILL-STM32F103C8T6_MODULE.P$38 (5V), D4.A, IC3.1 (VO), J15.18
A_HIGH: BLUEPILL-STM32F103C8T6_MODULE.P$34 (PB6/SCL1), IC2.12 (HIN), J15.14
A_LOW: BLUEPILL-STM32F103C8T6_MODULE.P$12 (PA7/A1/M0SI1), J14.12, R16.2
BEMF_PHASE_A: BLUEPILL-STM32F103C8T6_MODULE.P$6 (PA1/A7), C16.2, J14.6, R8.1, R27.2
BEMF_PHASE_B: BLUEPILL-STM32F103C8T6_MODULE.P$7 (PA2/A6/TX2), C12.2, J14.7, R11.2, R15.2
BEMF_PHASE_C: BLUEPILL-STM32F103C8T6_MODULE.P$8 (PA3/A5/RX2), C8.2, J14.8, R7.2, R20.2
B_HIGH: BLUEPILL-STM32F103C8T6_MODULE.P$35 (PB7/SDA1), J11.1, J15.15
B_HIGH_J0: IC5.12 (HIN), J11.2
B_LOW: BLUEPILL-STM32F103C8T6_MODULE.P$13 (PB0/A0), IC5.14 (LIN), J14.13
C_HIGH: BLUEPILL-STM32F103C8T6_MODULE.P$36 (PB8), IC1.12 (HIN), J15.16
C_LOW: BLUEPILL-STM32F103C8T6_MODULE.P$14 (PB1), J1.1, J14.14
C_LOW_J1: IC1.14 (LIN), J1.2
GND: BLUEPILL-STM32F103C8T6_MODULE.P$19 (GND/1), BLUEPILL-STM32F103C8T6_MODULE.P$20 (GND/2), BLUEPILL-STM32F103C8T6_MODULE.P$39 (GND/3), C1.1, C2.1, C3.1, C4.1, C8.1, C9.1, C10.1, C12.1, C13.1, C14.1, C16.1, C18.1, C19.1, C20.1, IC1.2 (COM), IC1.15 (VSS), IC2.2 (COM), IC2.15 (VSS), IC3.2 (GND), IC4.2 (V-), IC5.2 (COM), IC5.15 (VSS), J14.19, J14.20, J15.19, JP1.3, R4.1, R7.1, R12.1, R15.1, R24.1, R27.1, R29.2, R31.2, R32.1, R36.2
HS_FL.SUP_A: C15.1, D3.C, IC2.7 (VB)
HS_FL.SUP_B: C11.1, D2.C, IC5.7 (VB)
HS_FL.SUP_C_: C5.1, D1.C, IC1.7 (VB)
unnamed: R1.2, R5.2, U$1.4 (G)
unnamed: J3.2, R9.1
unnamed: R2.2, R6.1, U$1.2 (G)
unnamed: IC1.8 (HO), R1.1
unnamed: J2.2, R2.1
unnamed: IC1.1 (LO), J2.1
unnamed: R8.2, R23.2
unnamed: R3.2, R20.1
unnamed: R9.2, R13.2, U$16.4 (G)
unnamed: IC5.8 (HO), J3.1
unnamed: R10.2, R14.1, U$16.2 (G)
unnamed: J4.2, R10.1
unnamed: IC5.1 (LO), J4.1
unnamed: IC4.4 (-IN), R32.2, R33.1
unnamed: R21.2, R25.2, U$10.4 (G)
unnamed: R22.2, R26.1, U$10.2 (G)
unnamed: IC2.8 (HO), R21.1
unnamed: R22.1, R28.2
unnamed: IC2.1 (LO), R28.1
unnamed: IC4.1 (OUT), R33.2, R34.1
unnamed: BLUEPILL-STM32F103C8T6_MODULE.P$5 (PA0/A8), J14.5
unnamed: IC2.14 (LIN), R16.1
unnamed: J9.1, R35.2
unnamed: BLUEPILL-STM32F103C8T6_MODULE.P$26 (PA9/TX1), J15.6, JP1.2
unnamed: BLUEPILL-STM32F103C8T6_MODULE.P$27 (PA10/RX1), J15.7, JP1.1
unnamed: IC4.3 (+IN), R29.1, R37.1
unnamed: BLUEPILL-STM32F103C8T6_MODULE.P$1 (VBAT), J14.1
unnamed: BLUEPILL-STM32F103C8T6_MODULE.P$2 (PC13), J14.2
unnamed: BLUEPILL-STM32F103C8T6_MODULE.P$3 (PC14), J14.3
unnamed: BLUEPILL-STM32F103C8T6_MODULE.P$4 (PC15), J14.4
unnamed: BLUEPILL-STM32F103C8T6_MODULE.P$11 (PA6/A2/MISO1), J14.11
unnamed: BLUEPILL-STM32F103C8T6_MODULE.P$15 (PB10/TX3/SCL2), J14.15
unnamed: BLUEPILL-STM32F103C8T6_MODULE.P$16 (PB11/RX3/SDA2), J14.16
unnamed: BLUEPILL-STM32F103C8T6_MODULE.P$17 (RESET), J14.17
unnamed: BLUEPILL-STM32F103C8T6_MODULE.P$21 (PB12/SS2), J15.1
unnamed: BLUEPILL-STM32F103C8T6_MODULE.P$22 (PB13/SCK2), J15.2
unnamed: BLUEPILL-STM32F103C8T6_MODULE.P$23 (PB14/MIS02), J15.3
unnamed: BLUEPILL-STM32F103C8T6_MODULE.P$24 (PB15/MOSI2), J15.4
unnamed: BLUEPILL-STM32F103C8T6_MODULE.P$25 (PA8), J15.5, JP1.4
unnamed: BLUEPILL-STM32F103C8T6_MODULE.P$28 (PA11/USB-), J15.8
unnamed: BLUEPILL-STM32F103C8T6_MODULE.P$29 (PA12/USB+), J15.9
unnamed: BLUEPILL-STM32F103C8T6_MODULE.P$30 (PA15), J15.10
unnamed: BLUEPILL-STM32F103C8T6_MODULE.P$31 (PB3), J15.11
unnamed: BLUEPILL-STM32F103C8T6_MODULE.P$32 (PB4), J15.12
unnamed: BLUEPILL-STM32F103C8T6_MODULE.P$33 (PB5), J15.13
unnamed: BLUEPILL-STM32F103C8T6_MODULE.P$37 (PB9), J15.17
unnamed: BLUEPILL-STM32F103C8T6_MODULE.P$40 (3V3/1), J15.20
PHASE_A: C15.2, IC2.6 (VS), PHASE_C.1, R23.1, R25.1, U$10.3 (S), U$10.7 (D), U$10.8 (D)
PHASE_B: J5.2, PHASE_B.1, R13.1, U$16.3 (S), U$16.7 (D), U$16.8 (D)
PHASE_BJ: C11.2, IC5.6 (VS), J5.1, R11.1
PHASE_C: C5.2, IC1.6 (VS), PHASE_A.1, R3.1, R5.1, U$1.3 (S), U$1.7 (D), U$1.8 (D)
SENSE_CURRENT_PA5: BLUEPILL-STM32F103C8T6_MODULE.P$10 (PA5/A3/SCK1), C19.2, J14.10, R34.2
SENSE_VIN: BLUEPILL-STM32F103C8T6_MODULE.P$9 (PA4/A4/SS1), J9.2, J14.9, R36.1
TOT_CURRENT: C6.2, C7.2, R6.2, R14.2, R26.2, R31.1, R37.2, U$1.1 (S), U$10.1 (S), U$16.1 (S)
VCC3.3V: BLUEPILL-STM32F103C8T6_MODULE.P$18 (3V3), C18.2, IC4.5 (V+), J14.18
VDD_LOGIC_4.4V: C3.2, C9.2, C20.2, D4.C, IC1.11 (VDD), IC2.11 (VDD), IC5.11 (VDD)
V_MOTOR: C1.2, C2.2, C4.2, C6.1, C7.1, C10.2, C13.2, C14.2, D1.A, D2.A, D3.A, IC1.3 (VCC), IC2.3 (VCC), IC3.3 (VI), IC5.3 (VCC), R35.1, U$1.5 (D), U$1.6 (D), U$10.5 (D), U$10.6 (D), U$16.5 (D), U$16.6 (D), V_MOTOR.1

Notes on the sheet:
Drawn at Grid = 0.635 mm = 0.025inch
It was for per phase current sens. R=0.0203 Ω PCB FR4 1 oz = 0.035 mm W=0.406 mm L=17 mm
Kamp need=~127 times for 0.02Ω shunt, Kamp=~51times for 0.05Ω|50mΩ shunt PCB Shunt 0.0203 Ω at PCB FR4 ,1 oz = 0.035 mm W=0.406 mm L=17 mm Kamp=(R29/R32) - see classical difference amplifier sch
The opamp should be w. lowest possible offset. Some of them: TLC277

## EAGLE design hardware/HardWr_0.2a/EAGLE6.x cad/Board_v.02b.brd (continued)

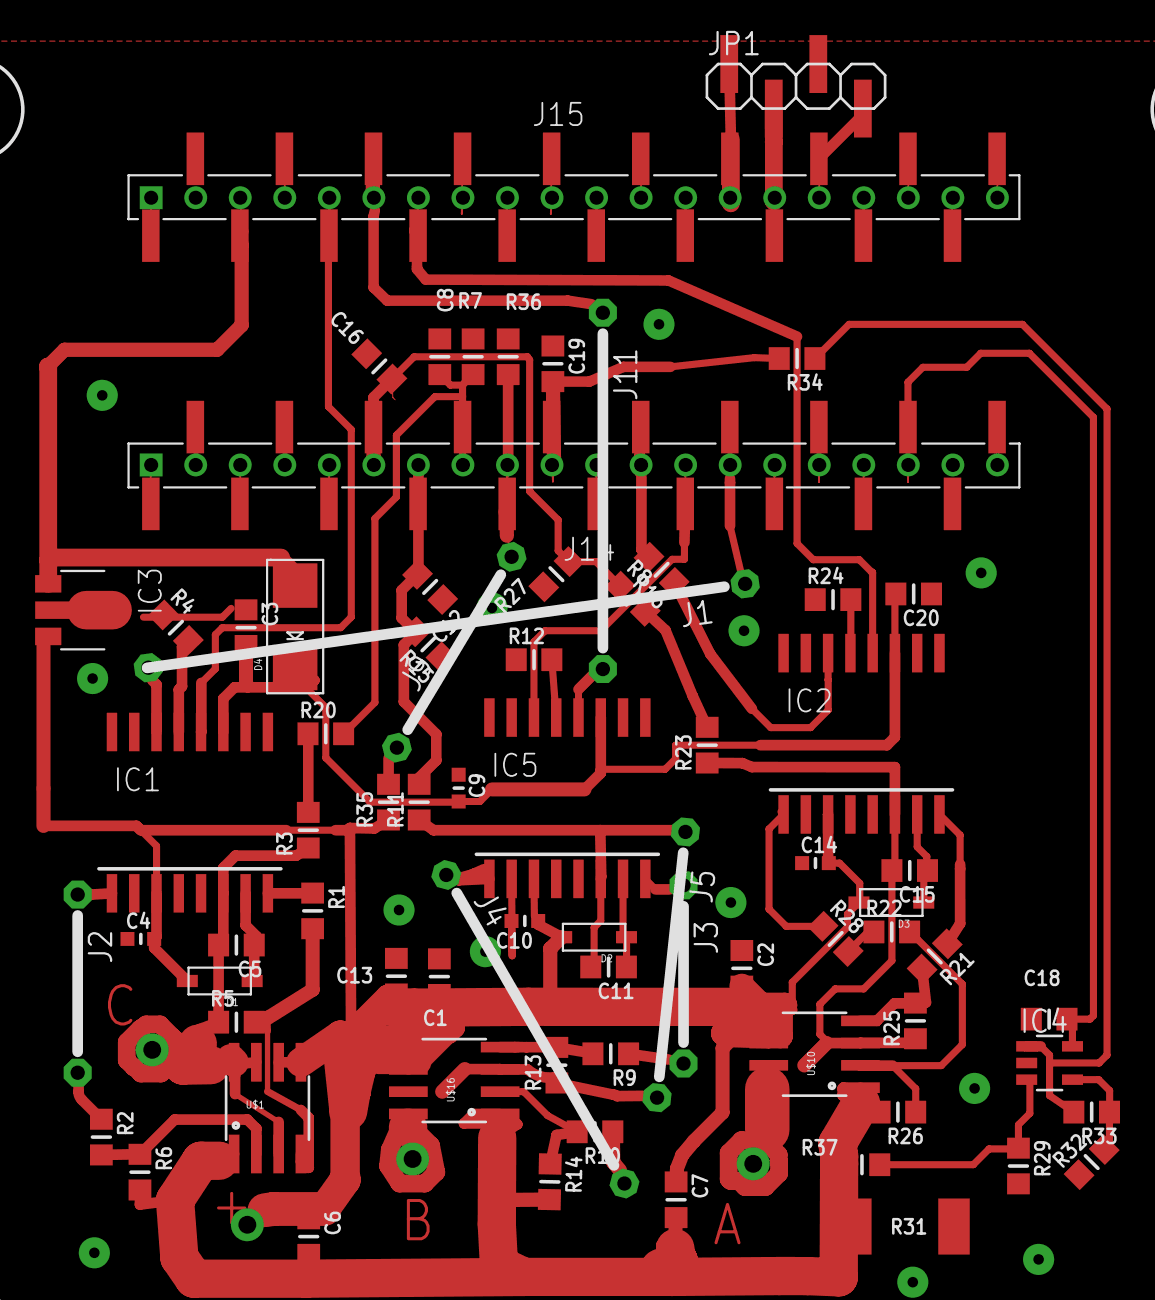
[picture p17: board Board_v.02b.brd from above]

Board: 2 copper layers, 83 parts (0 on the bottom side), 76 nets.

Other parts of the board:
U$11, U$12, U$13, U$21: MOUNTINGHOLE_2.8

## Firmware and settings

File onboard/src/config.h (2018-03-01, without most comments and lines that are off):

#define _CONFIG_H
#include "stdint.h"
#define DEFAULT_CONFIG_VERSION		2.03f	// This config format is *incompatible* with the original esc32 firmware
#define DEFAULT_STARTUP_MODE		0       // This is the run mode that the ESC defaults to when first powered on. 0 == normal open loop operation, 1 == closed loop RPM mode, 2 == closed loop thrust mode (not yet implemented)
#define DEFAULT_BAUD_RATE		230400  	// Allowable range 9600 to 921600
#define DEFAULT_ESC_ID			0			// if nothing else is written into the configuration page. Can be retrieved by index.
#define DEFAULT_rpmPID_P_TERM	2048       // was 0.25f in FP version. The P term for the RPM PI controller. You may want it ==4096
#define DEFAULT_PNFAC			10.0f		// ???
#define DEFAULT_rpmPID_I_TERM	10			// 0.0006f     // The I term for the RPM PI controller
#define DEFAULT_INFAC			0.15f		// ???
#define DEFAULT_FF1TERM			1.667189e-07 //+4.848572e-08     // Feed forward terms used for the RPM controller.  Closed loop RPM mode will not function until FF1 & FF2 terms have been set.
#define DEFAULT_FF2TERM			-3.752384e-04 //+1.144477e-03     // These values should be evaluated/calculated using the esc32Cal program with the –r2v option
#define DEFAULT_CL1TERM			+3.183795e+00     // CL1TERM through CL5TERM are used by the virtual current limiter which will not function until they are set.
#define DEFAULT_CL2TERM			+8.285745e-04     // If CL1TERM through CL5TERM is not set, a PI controller will be used for current limiting instead.
#define DEFAULT_CL3TERM			+1.429679e+01     // CL1TERM through CL5TERM can be calculated using the esc32Cal program with the –cl option.
#define DEFAULT_CL4TERM			+2.150966e-04     // see http://autoquad.org/wiki/wiki/aq-esc32/esc32/esc32-calibrations/
#define DEFAULT_CL5TERM			-1.420920e+01
#define DEFAULT_THR1TERM		0.0f
#define DEFAULT_THR2TERM		1.0f
#define DEFAULT_SHUNT_RESISTANCE_mOhm 20	   // in mili Ohms. The amplifier had default fixed gain of 50.9
#define DEFAULT_SHUNT_RESISTANCE_Ohm_x0x10000 1311 // (DEFAULT_SHUNT_RESISTANCE_mOhm * 65536)/1000 // scaled value. 1311 for Rshunt = 0.02 Ohm
#define DEFAULT_MIN_PERIOD			50.0f	    // The minimum commutation period allowed in microseconds
#define DEFAULT_MAX_PERIOD			12000.0f  	// The maximum commutation period allowed in microseconds
#define DEFAULT_BLANKING_MICROS			30.0f	// The number of microseconds to ignore back EMF after a commutation.
#define DEFAULT_ADVANCE				10.0f	    // The amount of timing advance in electrical degrees.  There are 60 electrical degrees in a commutation cycle.  This value can be set from 0 to 30 degrees.
#define DEFAULT_START_VOLTAGE			1.1f	// The amount of voltage presented to the motor during startup. Allowable range is 0.1v to 3.0v
#define DEFAULT_START_ALIGN_TIME		600	    // ms to align rotor in known position
#define DEFAULT_START_ALIGN_VOLTAGE		0.9f    // max voltage during align (around 0.8 * START_VOLTAGE)
#define DEFAULT_START_STEPS_NUM			0	    // steps without commutation
#define DEFAULT_START_STEPS_PERIOD	16000	    // time in us between steps
#define DEFAULT_START_STEPS_ACCEL		0	    // us each following step will be shorter (acceleration)
#define DEFAULT_N_GOOD_DETECTS_START	75		// 	Once started, the number of good/in order zero crossings needed to be detected before the motor is considered to be in the running state.
#define DEFAULT_N_BAD_DETECTS_DISARM	48		// The number of missed zero crossing detects allowed before the ESC considers the motor not to be running at which point will go into the disarmed state.
#define DEFAULT_MAX_CURRENT		0	    	// was 20.0. When set, the throttle limiter runs. The maximum amount of current in amps that the ESC will allow.
#define DEFAULT_FET_PWM_SWITCH_FREQ_KHZ	20	    // The output PWM pulse frequency used to power the motor windings in KHz.  Valid range is from 4KHz to 64KHz.
#define DEFAULT_MOTOR_POLES			 14     // The number of magnetic poles used in the motor’s construction.  This value only needs to be set correctly if you want to use the RPM closed loop mode.
#define DEFAULT_PWM_INTF_MIN_PERIOD		2200	// PWM interface: The minimum period in microseconds that the ESC will consider an input PWM waveform to be valid.  Default value represents approx 450Hz.  For MultiWii and ArduCopter APM need to be 2000
#define DEFAULT_PWM_INTF_MAX_PERIOD		25000	// PWM interface: The maximum period in microseconds that the ESC will consider an input PWM waveform to be valid.  Default value represents approx 40Hz
#define DEFAULT_PWM_INTF_MIN_VALUE		750	    // PWM interface: The minimum input PWM pulse length in microseconds which the ESC will consider to be valid. For DJI Naza this value has to be 900!
#define DEFAULT_PWM_INTF_LO_VALUE		1000	  // PWM interface: The input PWM pulse length in microseconds for the lowest throttle setting. For ArduCopter APM (or Open Pilot Revo w/ APM fw) this value needs to be changed to 1035!
#define DEFAULT_PWM_INTF_HI_VALUE		1950	  // PWM interface: The input PWM pulse length in microseconds for the highest throttle setting.
#define DEFAULT_PWM_INTF_MAX_VALUE		2250	  // PWM interface: The maximum input PWM pulse length in microseconds which the ESC will consider to be valid.
#define DEFAULT_PWM_INTF_MIN_START		1100	  // PWM interface: The input PWM pulse length in microseconds at which the motor will be started.  Once running, the throttle can be brought as low as PWM_MIN_VALUE as long as the motor does not stall.
#define DEFAULT_PWM_INTF_LOWPASS		0.0f	    // PWM interface: lowpass on PWM input values (0 = none, 10 = heavy, no upper limit)
#define DEFAULT_RPM_INTF_MEAS_LP		0.5f	    // PWM interface: lowpass measured RPM values for closed loop control (0 = none, 0.99 = max, >=1 not allowed)
#define DEFAULT_PWM_INTF_RPM_SCALE		6500	  // PWM interface: The scale of the input PWM pulse length.  In closed loop RPM run mode, PWM_LO_VALUE will indicate 0 RPM and PWM_HI_VALUE will indicate this RPM. Closed loop modes only! RPM equivalent of maximum PWM IN in CLOSED_LOOP mode
#define DEFAULT_FET_BRAKING			0         // Turns on regenerative braking in closed loop modes (experimental),  0 == off, 1 == on. Closed Loop modes only!!
#define DEFAULT_SERVO_DUTY			16.0f	  // % TODO: convert to promiles (percent * 10)
#define DEFAULT_SERVO_P				0.05f	  // TODO: convert to fixed point x1024..x32768 PID can withstand some precision loss
#define DEFAULT_SERVO_D				0.0f
#define DEFAULT_SERVO_MAX_RATE		1000.0f	  // deg/s TODO: convert to mrad/s
#define DEFAULT_SERVO_SCALE			360.0f	  // deg   TODO: convert to mrad, 1000 milliradian = 57.2957795131 deg
#define DEFAULT_DIRECTION			1	    // 1 == forward, -1 == reverse
#define FLASH_PAGE_SIZE			((uint16_t)0x400)   // 1024 bytes
#define FLASH_WRITE_ADDR		(0x08000000 + (uint32_t)FLASH_PAGE_SIZE * 63)    // use the last KB for storage, we assume 64 KB flash
#define ENABLE_ONEWIRE_PROTOCOL 1
#undef	ENABLE_ONEWIRE_PROTOCOL			// disable one wire protocol support
#define ENABLE_CANBUS_PROTOCOL 1
#undef	ENABLE_CANBUS_PROTOCOL			// disable CANBUS protocol support
#define ENABLE_PWM_PROTOCOL 1
#undef	ENABLE_PWM_PROTOCOL				// disable PWM control protocol support
#define USE_PWM_PIN_AS_USART_DEVICE_SELECT  1	// allow parallel connection of USART RX & TX lines with "chip select" line
enum configParameters {
    fCONFIG_VERSION = 0,
    uSTARTUP_MODE, // 0 == normal open loop mode 1 == closed loop RPM mode 2 == thrust closed loop mode
    uBAUD_RATE,    // The default baud rate
    uPTERM,        // Speed PI control, P item
    uITERM,        // Speed PI control, item I
    FF1TERM,	  // Feed forward terms used for the RPM controller.  Closed loop RPM mode will not function until FF1 & FF2 terms have been set.
    FF2TERM,
    CL1TERM,	  // Current Limiter (CL) coefficients. CL1TERM is in range []
    CL2TERM,	  // CL2TERM is in range []
    CL3TERM,	  // CL3TERM is in range []
    CL4TERM,	  // CL4TERM is in range []
    CL5TERM,	  // CL5TERM is in range []
    SHUNT_RESISTANCE_MILIOHM,
    fMIN_PERIOD,       // The minimum commutation period
    fMAX_PERIOD,		  // The maximum commutation period
    fBLANKING_MICROS,  // BEMF sensing blanking time
    ADVANCE,          // The amount of timing advance in electrical degrees.  There are 60 electrical degrees in a commutation cycle.  This value can be set from 0 to 30 degrees.
    fSTART_VOLTAGE,
    uGOOD_DETECTS_START, // how many good detects're necessary to consider motor running OK ?
    uBAD_DETECTS_DISARM, // how many bad detects are enough to stop the motor from running
    fMAX_CURRENT,
    uSWITCH_FREQ,        // PWM freq in KHz, default 20KHz
    uMOTOR_POLES,        // N of magnetic poles, used to detect RPM and ...
    PWM_INTF_MIN_PERIOD,
    PWM_INTF_MAX_PERIOD,
    PWM_INTF_MIN_VALUE,      // PWM input minimum high time (pulse width)
    PWM_INTF_LO_VALUE,
    PWM_INTF_HI_VALUE,
    PWM_INTF_MAX_VALUE,     //  maximum high time (pulse width)
    PWM_INTF_MIN_START,
    PWM_INTF_RPM_SCALE,
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

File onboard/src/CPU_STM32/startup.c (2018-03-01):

/** Startup C file - no assembly startup is needed for m3 cores :-)
 * \file startup.c
 * \brief STM32 (STM32F101 - STM32F103) vector table and startupcode
 * \details STM32 (STM32F101 - STM32F103) vector table and startupcode
 * \author Marten Petschke
 * \date 21.Aug.2012
 * \Modifications, comments - A.Genchev, date 17.May.2015 
 */


#include "stm32f10x.h" // Load CMSIS and peripheral library and configuration

//#include "printf.h" // debug support
/******************************************************************************
* chip: STM32F101VB
* compiler: yagarto-gcc 7.1
******************************************************************************/
// Linker provided symbols (addresses):
extern unsigned long __data_init_start;      // init value location in the flash. Start address for the initialization
											 // values of the .data section.
extern unsigned long __data_start;           // RAM Start address for the .data section
extern unsigned long __data_end;             // RAM End address for the .data section
extern unsigned long __bss_start;            // RAM Start address for the .bss section
extern unsigned long __bss_end;              // RAM End address for the .bss section
extern unsigned long __stack_start;		 	 // RAM @ end of physical RAM; main and intr stack end (from linker script)
// stack end is where the heap ends, because the stack grows backwards
extern void __libc_init_array(void);  		 // calls CTORS of static objects in C++. Not needed for "pure C"

/*
+=============================================================================+
| local declarations
+=============================================================================+
*/

void Reset_Handler(void) __attribute__((noreturn));
extern void main(void);

static void __Init_Data(void)
{
	unsigned long *source;
	unsigned long *destination;
	// default stack left to "__main_stack_end" so no change here..

	// Copying data from Flash to RAM  - Initialize .data section
	source = &__data_init_start; // provided by the linker script
	for (destination = &__data_start; destination < &__data_end;)
	{
		*(destination++) = *(source++);
	}
	// default zero to undefined variables //Zero-init .bss section
	for (destination = &__bss_start; destination < &__bss_end;)
	{
		*(destination++) = 0;
	}
	/* Call CTORS of static objects */
	// __libc_init_array(); // C++! Not needed for "pure C"
}


/*------------------------------------------------------------------------*//**
* \brief Default interrupt handler.
* \details Default interrupt handler, used for interrupts that don't have their
* own handler defined.
*//*-------------------------------------------------------------------------*/

//static void __Default_Handler(void) __attribute__ ((interrupt));
void __Default_Handler(void)
{	// 1. Determining Which Exception Handler is Executing (if triggered by IRQ) as per http://www.freertos.org/Debugging-Hard-Faults-On-Cortex-M-Microcontrollers.html
	// We load the number of the executing interrupt into register 2 (r2) before the infinite loop is entered:
	// System Control Block 0xE000ED04	ICSR - Interrupt Control and State Register
	volatile uint32_t int_no = SCB->ICSR & 0xFF;
	//asm(" mov r3, ICSR"); // Load the address of the interrupt control register into r3
	//asm(" ldr r2, [r3, #0]"); // Load the value of the interrupt control register into r2 from the address held in r3.
	//asm(" uxtb r2, r2"); // The interrupt number is in the least significant byte - clear all other bits.
	UNUSED_PARAMETER(int_no);
	while (1)
	{;
	}

}

/*
+=============================================================================+
| assign all unhandled interrupts to the default handler using weak linking w alias
+=============================================================================+
*/

// Non-maskable interrupt (RCC clock security system)
void NMI_Handler(void) __attribute__ ((interrupt, weak, alias("__Default_Handler")));

// All class of fault
void HardFault_Handler(void) __attribute__ ((interrupt, weak, alias("__Default_Handler")));

// Memory management
void MemManage_Handler(void) __attribute__ ((interrupt, weak, alias("__Default_Handler")));

// Pre-fetch fault, memory access fault
void BusFault_Handler(void) __attribute__ ((interrupt, weak, alias("__Default_Handler")));

// Undefined instruction or illegal state
void UsageFault_Handler(void) __attribute__ ((interrupt, weak, alias("__Default_Handler")));

// Reserved 0x1C
void __Reserved_0x1C_Handler(void) __attribute__ ((interrupt, weak, alias("__Default_Handler")));

// Reserved 0x20
void __Reserved_0x20_Handler(void) __attribute__ ((interrupt, weak, alias("__Default_Handler")));

// Reserved 0x24
void __Reserved_0x24_Handler(void) __attribute__ ((interrupt, weak, alias("__Default_Handler")));

// Reserved 0x28
void __Reserved_0x28_Handler(void) __attribute__ ((interrupt, weak, alias("__Default_Handler")));

// System service call via SWI instruction
void SVC_Handler(void) __attribute__ ((interrupt, weak, alias("__Default_Handler")));

// Debug monitor
void DebugMon_Handler(void) __attribute__ ((interrupt, weak, alias("__Default_Handler")));

// Reserved 0x34
void __Reserved_0x34_Handler(void) __attribute__ ((interrupt, weak, alias("__Default_Handler")));

// Pendable request for system service
void PendSV_Handler(void) __attribute__ ((interrupt, weak, alias("__Default_Handler")));

// System tick timer
void SysTick_Handler(void) __attribute__ ((interrupt, weak, alias("__Default_Handler")));

// Window watchdog interrupt
void WWDG_IRQHandler(void) __attribute__ ((interrupt, weak, alias("__Default_Handler")));

// PVD through EXTI line detection interrupt
void PVD_IRQHandler(void) __attribute__ ((interrupt, weak, alias("__Default_Handler")));

// Tamper interrupt
void TAMPER_IRQHandler(void) __attribute__ ((interrupt, weak, alias("__Default_Handler")));

// RTC global interrupt
void RTC_IRQHandler(void) __attribute__ ((interrupt, weak, alias("__Default_Handler")));

// Flash global interrupt
void FLASH_IRQHandler(void) __attribute__ ((interrupt, weak, alias("__Default_Handler")));

// RCC global interrupt
void RCC_IRQHandler(void) __attribute__ ((interrupt, weak, alias("__Default_Handler")));

// EXTI Line0 interrupt
void EXTI0_IRQHandler(void) __attribute__ ((interrupt, weak, alias("__Default_Handler")));

// EXTI Line1 interrupt
void EXTI1_IRQHandler(void) __attribute__ ((interrupt, weak, alias("__Default_Handler")));

// EXTI Line2 interrupt
void EXTI2_IRQHandler(void) __attribute__ ((interrupt, weak, alias("__Default_Handler")));

// EXTI Line3 interrupt
void EXTI3_IRQHandler(void) __attribute__ ((interrupt, weak, alias("__Default_Handler")));

// EXTI Line4 interrupt
void EXTI4_IRQHandler(void) __attribute__ ((interrupt, weak, alias("__Default_Handler")));

// DMA1 Channel1 global interrupt
void DMA1_Channel1_IRQHandler(void) __attribute__ ((interrupt, weak, alias("__Default_Handler")));

// DMA1 Channel2 global interrupt
void DMA1_Channel2_IRQHandler(void) __attribute__ ((interrupt, weak, alias("__Default_Handler")));

// DMA1 Channel3 global interrupt
void DMA1_Channel3_IRQHandler(void) __attribute__ ((interrupt, weak, alias("__Default_Handler")));

// DMA1 Channel4 global interrupt
void DMA1_Channel4_IRQHandler(void) __attribute__ ((interrupt, weak, alias("__Default_Handler")));

// DMA1 Channel5 global interrupt
void DMA1_Channel5_IRQHandler(void) __attribute__ ((interrupt, weak, alias("__Default_Handler")));

// DMA1 Channel6 global interrupt
void DMA1_Channel6_IRQHandler(void) __attribute__ ((interrupt, weak, alias("__Default_Handler")));

// DMA1 Channel7 global interrupt
void DMA1_Channel7_IRQHandler(void) __attribute__ ((interrupt, weak, alias("__Default_Handler")));

// ADC1 and ADC2 global interrupt
void ADC1_2_IRQHandler(void) __attribute__ ((interrupt, weak, alias("__Default_Handler")));

// USB high priority or CAN TX interrupts:  different names for coocox and *** 
//void USB_HP_CAN_TX_IRQHandler(void) __attribute__ ((interrupt, weak, alias("__Default_Handler")));
void USB_HP_CAN1_TX_IRQHandler(void) __attribute__ ((interrupt, weak, alias("__Default_Handler")));


// USB low priority or CAN RX0 interrupts:  different names for coocox and ***
//void USB_LP_CAN_RX0_IRQHandler(void) __attribute__ ((interrupt, weak, alias("__Default_Handler")));
void USB_LP_CAN1_RX0_IRQHandler(void) __attribute__ ((interrupt, weak, alias("__Default_Handler")));



// CAN RX1 interrupt
void CAN_RX1_IRQHandler(void) __attribute__ ((interrupt, weak, alias("__Default_Handler")));

// CAN SCE interrupt
void CAN_SCE_IRQHandler(void) __attribute__ ((interrupt, weak, alias("__Default_Handler")));

// EXTI Line[9:5] interrupts
void EXTI9_5_IRQHandler(void) __attribute__ ((interrupt, weak, alias("__Default_Handler")));

// TIM1 break interrupt
void TIM1_BRK_IRQHandler(void) __attribute__ ((interrupt, weak, alias("__Default_Handler")));

// TIM1 update interrupt
void TIM1_UP_IRQHandler(void) __attribute__ ((interrupt, weak, alias("__Default_Handler")));

// TIM1 trigger and commutation interrupts
void TIM1_TRG_COM_IRQHandler(void) __attribute__ ((interrupt, weak, alias("__Default_Handler")));

// TIM1 capture compare interrupt
void TIM1_CC_IRQHandler(void) __attribute__ ((interrupt, weak, alias("__Default_Handler")));

// TIM2 global interrupt
void TIM2_IRQHandler(void) __attribute__ ((interrupt, weak, alias("__Default_Handler")));

// TIM3 global interrupt
void TIM3_IRQHandler(void) __attribute__ ((interrupt, weak, alias("__Default_Handler")));

// TIM4 global interrupt
void TIM4_IRQHandler(void) __attribute__ ((interrupt, weak, alias("__Default_Handler")));

// I2C1 event interrupt
void I2C1_EV_IRQHandler(void) __attribute__ ((interrupt, weak, alias("__Default_Handler")));

// I2C1 error interrupt
void I2C1_ER_IRQHandler(void) __attribute__ ((interrupt, weak, alias("__Default_Handler")));

// I2C2 event interrupt
void I2C2_EV_IRQHandler(void) __attribute__ ((interrupt, weak, alias("__Default_Handler")));

// I2C2 error interrupt
void I2C2_ER_IRQHandler(void) __attribute__ ((interrupt, weak, alias("__Default_Handler")));

// SPI1 global interrupt
void SPI1_IRQHandler(void) __attribute__ ((interrupt, weak, alias("__Default_Handler")));

// SPI2 global interrupt
void SPI2_IRQHandler(void) __attribute__ ((interrupt, weak, alias("__Default_Handler")));

// USART1 global interrupt
void USART1_IRQHandler(void) __attribute__ ((interrupt, weak, alias("__Default_Handler")));

// USART2 global interrupt
void USART2_IRQHandler(void) __attribute__ ((interrupt, weak, alias("__Default_Handler")));

// USART3 global interrupt
void USART3_IRQHandler(void) __attribute__ ((interrupt, weak, alias("__Default_Handler")));

// EXTI Line[15:10] interrupts
void EXTI15_10_IRQHandler(void) __attribute__ ((interrupt, weak, alias("__Default_Handler")));

// RTC alarm through EXTI line interrupt
void RTCAlarm_IRQHandler(void) __attribute__ ((interrupt, weak, alias("__Default_Handler")));

// USB wakeup from suspend through EXTI line interrupt:
void USBWakeUp_IRQHandler(void) __attribute__ ((interrupt, weak, alias("__Default_Handler")));



// TIM8 break interrupt
void TIM8_BRK_IRQHandler(void) __attribute__ ((interrupt, weak, alias("__Default_Handler")));

// TIM8 update interrupt
void TIM8_UP_IRQHandler(void) __attribute__ ((interrupt, weak, alias("__Default_Handler")));

// TIM8 trigger and commutation interrupts
void TIM8_TRG_COM_IRQHandler(void) __attribute__ ((interrupt, weak, alias("__Default_Handler")));

// TIM8 capture compare interrupt
void TIM8_CC_IRQHandler(void) __attribute__ ((interrupt, weak, alias("__Default_Handler")));

// ADC3 global interrupt
void ADC3_IRQHandler(void) __attribute__ ((interrupt, weak, alias("__Default_Handler")));

// FSMC global interrupt
void FSMC_IRQHandler(void) __attribute__ ((interrupt, weak, alias("__Default_Handler")));

// SDIO global interrupt
void SDIO_IRQHandler(void) __attribute__ ((interrupt, weak, alias("__Default_Handler")));

// TIM5 global interrupt
void TIM5_IRQHandler(void) __attribute__ ((interrupt, weak, alias("__Default_Handler")));

// SPI3 global interrupt
void SPI3_IRQHandler(void) __attribute__ ((interrupt, weak, alias("__Default_Handler")));

// UART4 global interrupt
void UART4_IRQHandler(void) __attribute__ ((interrupt, weak, alias("__Default_Handler")));

// UART5 global interrupt
void UART5_IRQHandler(void) __attribute__ ((interrupt, weak, alias("__Default_Handler")));

// TIM6 global interrupt
void TIM6_IRQHandler(void) __attribute__ ((interrupt, weak, alias("__Default_Handler")));

// TIM7 global interrupt
void TIM7_IRQHandler(void) __attribute__ ((interrupt, weak, alias("__Default_Handler")));

// DMA2 Channel1 global interrupt
void DMA2_Channel1_IRQHandler(void) __attribute__ ((interrupt, weak, alias("__Default_Handler")));

// DMA2 Channel2 global interrupt
void DMA2_Channel2_IRQHandler(void) __attribute__ ((interrupt, weak, alias("__Default_Handler")));

// DMA2 Channel3 global interrupt
void DMA2_Channel3_IRQHandler(void) __attribute__ ((interrupt, weak, alias("__Default_Handler")));

// DMA2 Channel4 and DMA2 Channel5 global interrupts
void DMA2_Channel4_5_IRQHandler(void) __attribute__ ((interrupt, weak, alias("__Default_Handler")));

/*
+=============================================================================+
| Vector table,  ".vectors" must be defined in linker script
| This table covers the very first 8 bytes in the Flash. They contain a
| stack address and a jump address to the first code - Reset_handler()
+=============================================================================+
Note: there are some extra handlers at the end, not for STM32F103C8
Note: the table name below(g_ISR_Vectors) must be the same as in the linker script used !!!
*/

void (* const g_ISR_Vectors[])(void) __attribute__ ((section(".g_ISR_Vectors"))) =
{
		(void (*)(void))&__stack_start, // Main stack end address, by default loaded in CONTROL special register
		Reset_Handler,						// first code after Reset
		NMI_Handler,						// Non-maskable interrupt (RCC clock security system)
		HardFault_Handler,					// All class of fault
		MemManage_Handler,					// Memory management
		BusFault_Handler,					// Pre-fetch fault, memory access fault
		UsageFault_Handler,					// Undefined instruction or illegal state
		__Reserved_0x1C_Handler,			// Reserved 0x1C
		__Reserved_0x20_Handler,			// Reserved 0x20
		__Reserved_0x24_Handler,			// Reserved 0x24
		__Reserved_0x28_Handler,			// Reserved 0x28
		SVC_Handler,						// System service call via SWI instruction
		DebugMon_Handler,					// Debug monitor
		__Reserved_0x34_Handler,			// Reserved 0x34
		PendSV_Handler,						// Pendable request for system service
		SysTick_Handler,					// System tick timer
		WWDG_IRQHandler,					// Window watchdog interrupt
		PVD_IRQHandler,						// PVD through EXTI line detection interrupt
		TAMPER_IRQHandler,					// Tamper interrupt
		RTC_IRQHandler,						// RTC global interrupt
		FLASH_IRQHandler,					// Flash global interrupt
		RCC_IRQHandler,						// RCC global interrupt
		EXTI0_IRQHandler,					// EXTI Line0 interrupt
		EXTI1_IRQHandler,					// EXTI Line1 interrupt
		EXTI2_IRQHandler,					// EXTI Line2 interrupt
		EXTI3_IRQHandler,					// EXTI Line3 interrupt
		EXTI4_IRQHandler,					// EXTI Line4 interrupt
		DMA1_Channel1_IRQHandler,			// DMA1 Channel1 global interrupt
		DMA1_Channel2_IRQHandler,			// DMA1 Channel2 global interrupt
		DMA1_Channel3_IRQHandler,			// DMA1 Channel3 global interrupt
		DMA1_Channel4_IRQHandler,			// DMA1 Channel4 global interrupt
		DMA1_Channel5_IRQHandler,			// DMA1 Channel5 global interrupt
		DMA1_Channel6_IRQHandler,			// DMA1 Channel6 global interrupt
		DMA1_Channel7_IRQHandler,			// DMA1 Channel7 global interrupt
		ADC1_2_IRQHandler,					// ADC1 and ADC2 global interrupt
		USB_HP_CAN1_TX_IRQHandler,// USB_HP_CAN_TX_IRQHandler,			// USB high priority or CAN TX interrupts
		USB_LP_CAN1_RX0_IRQHandler,// USB_LP_CAN_RX0_IRQHandler,			// USB low priority or CAN RX0 interrupts
		CAN_RX1_IRQHandler,					// CAN RX1 interrupt
		CAN_SCE_IRQHandler,					// CAN SCE interrupt
		EXTI9_5_IRQHandler,					// EXTI Line[9:5] interrupts
		TIM1_BRK_IRQHandler,				// TIM1 break interrupt
		TIM1_UP_IRQHandler,					// TIM1 update interrupt
		TIM1_TRG_COM_IRQHandler,			// TIM1 trigger and commutation interrupts
		TIM1_CC_IRQHandler,					// TIM1 capture compare interrupt
		TIM2_IRQHandler,					// TIM2 global interrupt
		TIM3_IRQHandler,					// TIM3 global interrupt
		TIM4_IRQHandler,					// TIM4 global interrupt
		I2C1_EV_IRQHandler,					// I2C1 event interrupt
		I2C1_ER_IRQHandler,					// I2C1 error interrupt
		I2C2_EV_IRQHandler,					// I2C2 event interrupt
		I2C2_ER_IRQHandler,					// I2C2 error interrupt
		SPI1_IRQHandler,					// SPI1 global interrupt
		SPI2_IRQHandler,					// SPI2 global interrupt
		USART1_IRQHandler,					// USART1 global interrupt
		USART2_IRQHandler,					// USART2 global interrupt
		USART3_IRQHandler,					// USART3 global interrupt
		EXTI15_10_IRQHandler,				// EXTI Line[15:10] interrupts
		RTCAlarm_IRQHandler,				// RTC alarm through EXTI line interrupt
		USBWakeUp_IRQHandler,//USBWakeup_IRQHandler,				// USB wakeup from suspend through EXTI line interrupt
		TIM8_BRK_IRQHandler,				// TIM8 break interrupt
		TIM8_UP_IRQHandler,					// TIM8 update interrupt
		TIM8_TRG_COM_IRQHandler,			// TIM8 trigger and commutation interrupts
		TIM8_CC_IRQHandler,					// TIM8 capture compare interrupt
		ADC3_IRQHandler,					// ADC3 global interrupt
		FSMC_IRQHandler,					// FSMC global interrupt
		SDIO_IRQHandler,					// SDIO global interrupt
		TIM5_IRQHandler,					// TIM5 global interrupt
		SPI3_IRQHandler,					// SPI3 global interrupt
		UART4_IRQHandler,					// UART4 global interrupt
		UART5_IRQHandler,					// UART5 global interrupt
		TIM6_IRQHandler,					// TIM6 global interrupt
		TIM7_IRQHandler,					// TIM7 global interrupt
		DMA2_Channel1_IRQHandler,			// DMA2 Channel1 global interrupt
		DMA2_Channel2_IRQHandler,			// DMA2 Channel2 global interrupt
		DMA2_Channel3_IRQHandler,			// DMA2 Channel3 global interrupt
		DMA2_Channel4_5_IRQHandler,			// DMA2 Channel4 and DMA2 Channel5 global interrupts
		(void *)0xF108F85F   // hardcoded instruction:
		// 0x20000109 <__vector_table+265>: ldr.w pc, [pc, #-264] ; 0x20000004
		// This is for boot in RAM mode for  STM32F10x Medium Density devices.
		// loads the value at 0x2000004 into the PC register and starts running from it (reset handler).
};



/*
+=============================================================================+
| Reset_Handler() - first code after reset. Interrupts are disabled.
+=============================================================================+
*/
extern void _start();
void __attribute__((noreturn)) Reset_Handler(void)
{	// notice the lack of local variables - these would permanently reserve space on the stack
	// and I prefer to trade code memory (flash) for RAM
	// VTOR stuff happens automatically - depending on the linker, just load .elf
	// SCB->VTOR = (unsigned int) & g_ISR_Vectors;
	//asm(" bkpt ");
	// http://embdev.net/topic/185672:
	// A.Genchev: We reset stack pointer: basically this is *NOT* necessary, because we loose only 4 bytes stack memory - despite "noreturn" flag,
	// GCC has pushed one register (r7) into the stack.
	// To restore the lost 32 bits, we put in more bits in code. Also this code helps me when I debug from RAM.
	asm(" LDR r0, =__stack_start"); // Load stack start address into r0
	asm(" MSR msp, r0"); // r0 -> r13

	/* SCB's VTOR register to the correct interrupt-vector-table address in ram
	 * Vector_Table_Base is defined in misc.h as follows:
	#define NVIC_VectTab_RAM             ((uint32_t)0x20000000)
	#define NVIC_VectTab_FLASH           ((uint32_t)0x08000000)
	*/
	// This is necessary to work the interrupts:
	#ifdef VECT_TAB_SRAM
	    NVIC_SetVectorTable(NVIC_VectTab_RAM,0X0);
	#endif
	__Init_Data();
	SystemInit(); // // Setup STM32 system (clock, PLL and Flash configuration)
	//init_UART1(); // printf support
	//_start(); // c library start. absent/not linked in if "-nostdlib" switch used on linker
	main(); // starting main program

	while(1){} // no-return
}

/******************************************************************************
* END OF FILE
******************************************************************************/

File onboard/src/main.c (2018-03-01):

/*
    This file is part of AutoQuad ESC32.

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
    Copyright © 2011, 2012, 2013  Bill Nesbitt
    
    Modified 2016-2018 by A.Genchev
*/

#include "main.h"

#include "adc.h"
#include "rcc.h"
#include "config.h"
#include "timer.h"
#include "fet.h"
#include "serial.h"
#include "pwm.h"
#include "run.h"
#include "cli.h"
#include "binary.h"
#ifdef ENABLE_ONEWIRE // please, define which protocols are enabled in config.h
#include "ow.h"
#endif //ENABLE_ONEWIRE
#include "can.h"
#include "GPIO.h"

// these are accessed both in main() and IRQ handler SysTick_Handler:
volatile uint32_t minCycles, idleCounter, totalCycles; // The total number of cycles is used to calculate the percentage of free time (that is, without interruption, nops in the loop)
volatile escStates_t ESC_state;
volatile uint8_t inputMode; // Run status, input mode (control mode serial port iic can pwm 1wire)


int main(void)
{
	rccInit();   // Turn on some of the CPU clocks by default
	NVIC_PriorityGroupConfig(NVIC_PriorityGroup_4); // 4 bits for preempt priority 0 bit for sub priority
	//
	GPIO_Init_PP_Output_Low(GPIO_STATUS_LED_PORT, GPIO_STATUS_LED_PIN); //statusLed = digitalInit(GPIO_STATUS_LED_PORT, GPIO_STATUS_LED_PIN);
	GPIO_Init_PP_Output_Low(GPIO_ERROR_LED_PORT, GPIO_ERROR_LED_PIN); //errorLed = digitalInit(GPIO_ERROR_LED_PORT, GPIO_ERROR_LED_PIN);
#ifdef ESC_DEBUG
	GPIO_Init_PP_Output_Low(GPIO_TP_PORT, GPIO_TP_PIN);
	// digitalLo(tp); - done by digitalInit()
#endif

	timerInit();  // Timer2 internal counter
	configInit();  // load the default configuration
	adcInit();
	fetInit();
	serialInit();
#ifdef 	ENABLE_CANBUS_PROTOCOL // see config.h for these defines
	canInit();    // CAN bus (since version 1.5)
#endif	//ENABLE_CANBUS_PROTOCOL
	runInit();
	cliInit();
#ifdef ENABLE_ONEWIRE
	owInit();     // initialize the 1-wire protocol
#endif
	runDisarm(REASON_STARTUP);  // initial state - disarmed
	inputMode = ESC_INPUT_PWM;  // default mode - to be compatible w other ESCs

	fetSetDutyCycle(0);
	fetBeep(200, 100);
	fetBeep(300, 100);
	fetBeep(400, 100);
	fetBeep(500, 100);
	fetBeep(400, 100);
	fetBeep(300, 100);
	fetBeep(200, 100);
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

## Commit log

2017-11-25 Different makefile
    Compiles the ESC firmware with a GNU arm-none-eabi toolchain.
2017-11-25 Refactoring of the project to have cleaner layout
    [esc32_motor_db.xml]
2017-11-25 Code rework. Add all necessary routines to compile w GCC
    [esc32_motor_db.xml]
2018-02-25 Update Readme.md
    added hardware schematics

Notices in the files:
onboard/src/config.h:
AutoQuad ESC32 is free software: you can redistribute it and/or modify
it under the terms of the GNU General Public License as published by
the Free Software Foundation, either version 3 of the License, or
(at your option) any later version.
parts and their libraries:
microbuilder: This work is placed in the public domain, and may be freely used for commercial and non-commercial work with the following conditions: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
